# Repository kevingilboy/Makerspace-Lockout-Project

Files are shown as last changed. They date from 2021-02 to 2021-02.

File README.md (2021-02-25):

# Makerspace Lockout Project
Makerspace staff exert much of their time watching over students and verifying safety training… a process that is mundane, imperfect, and begs for automation.
Our motivation was to non-obtrusively enforce the safe and sustainable use of machinery in the Makerspaces across campus through RF student ID verification against a user database - if a student is not trained, power is cut to the tool and it will not turn on. If a student is trained, the tool is enabled.

[Video](https://www.youtube.com/watch?v=2HG-vyV4yoM)

[Poster](https://github.com/kevingilboy/Makerspace-Lockout-Project/blob/main/Design%20Expo%20Poster.pdf)

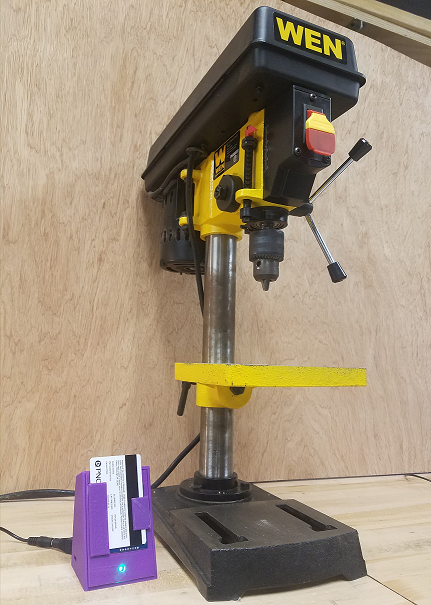
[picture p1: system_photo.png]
System Photo


## System Usage Diagram
The system is diagrammed below. A Raspberry Pi acts as a Wi-Fi access point and MQTT broker for Arduino microcontrollers in the Makerspace, and it communicates with the external database to authenticate users trying to enable tools. The complete workflow is as follows (please watch the [Video](https://www.youtube.com/watch?v=2HG-vyV4yoM) above for the simpler workflow. It is much easier to "show" this project than to "tell" about it).
1. A user inserts their ID into the 3D printed "Card Holder". The Holder holds the card such that the RFID element hovers over an RFID reader. A Wi-Fi Arduino inside the Holder detects that a card has been placed and reads the UUID from the student ID.
2. The Wi-Fi Arduino publishes a MQTT message to the Raspberry Pi in the room asking for user authentication, and notifies it which tool the user is trying to use. The Arduino changes a status LED to yellow to signify that authentication is underway.
3. The Pi asks the main Makerspace server if the user is authenticated for the given tool and the server responds.
4. An optional buddy system is also supported in that a tool can require a room administrator to put their card in a separate "buddy" Card Holder.
5. If authenticated (and a buddy is present if required), the Pi publishes a MQTT message to a separate Wi-Fi Arduino that controls power to the tool via a 120V relay. The Card Holder Arduino also receives this message and changes the status LED to green to signify that the user is authenticated.
6. The Arduino enables the tool through the relay and the user can do their work. The system can detect if the tool is prematurely switched on as it turns on the relay (e.g. if the previous person forgot to turn off the tool and simply grabbed their ID and left), and quickly switches the relay off as a failsafe. A buzzer makes noise to let the user know to switch off the tool for the relay to be enabled.
7. If a user leaves their ID on a Card Reader but does not power on the machine for a certain time threshold, an email is sent to them stating that they either forgot their ID on the Card Reader or are being unsafe by leaving tools enabled and unused for long periods of time.
8. When the user is finished, they take their ID off the Card Reader, which turns the status light to red and triggers a MQTT message from the Card Reader to the Pi, which then publishes a MQTT message to the relay-controlling Arduino to turn off the relay. If the user takes their ID off the reader without switching off the tool (as detected through current monitoring), a buzzer makes noise and power to the relay is cut.

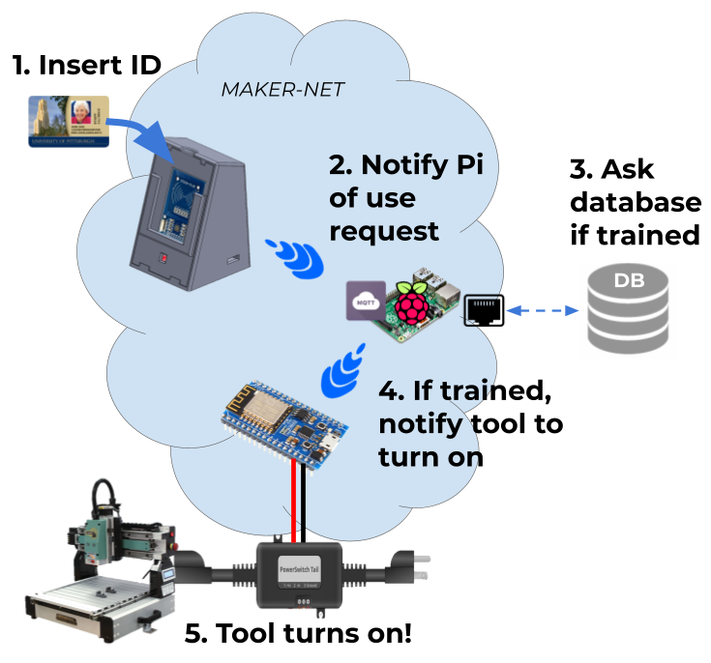
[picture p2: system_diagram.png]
System Diagram


## Materials for One Connected Tool
| Component | Quantity | Total Cost
| --- | --- | ---
| Wi-Fi Arduino MCU (ESP8266) | 2 | $20
| RFID Reader (MFRC522) | 1 | $5
| RGB LED (Adafruit Neopixel) | 1 | $1
| Relay (PowerSwitch Tail II) | 1 | $26
| Current Sensor (30A Split Core from Sparkfun) | 1 | $10
| Piezo Alarm (Optional) | 1 | $3
| Power supply for MCUs | 2 | $10
| Assorted jumpers | |
| PCB board | |
| 3D printer filament | |
| Some sort of metal lock box? | |
| | | $75

## Materials for One Connected Makerspace
| Component | Quantity | Total Cost
| --- | --- | -----
| Raspberry Pi 3 | 1 | $35
| 2A Wall Adapter Power Supply (USB Micro-B) |1 | $8
| | | $43

## State of the Repo
All arduino code has been uploaded

All EAGLE PCB CAD files have been uploaded

All SolidWorks CAD files have been uploaded

In-Room Pi Access Point files have been uploaded - SD card image available by request

The Database has been defined but the external server code has not been uploaded

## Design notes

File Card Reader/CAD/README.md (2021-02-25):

# CAD

There are three 3D-printable parts for the housing shown below, which was designed by BryanPatrick (baf56@pitt.edu).
- The body, which is a hollowed container with an exposed front meant to house the ESP8266 arduino and wiring. A slot is cutout on the top to allow removal of the pressfit lid (see below) and on the side to allow a power cord to reach the arduino.
- The lid, which is a pressfit cap for the hollow body. It has a slot for a neopixel and RFID reader to pressfit into. It also has slots for the U shape holder to pressfit into (see below)
- The U shape holder, which is meant to hold a student ID at the perfect height so that the embedded RFID element is aligned with the RFID sensor when seated in the holder. The bottom is open to allow sawdust or other particulate to fall right through.

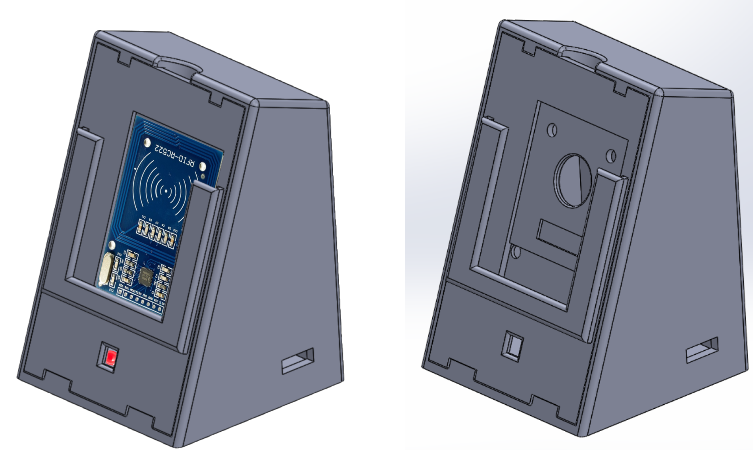
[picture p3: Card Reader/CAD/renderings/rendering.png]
Rendering


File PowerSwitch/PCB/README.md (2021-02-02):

# PCB

The PCB EAGLE CAD files are included here. The PCB was milled using an Othermill (Bantam CNC) with a 1/64" tool.

The ESP8266 arduino was soldered to this PCB, along with the current sensor, powertail relay, buzzer, and some resistors.

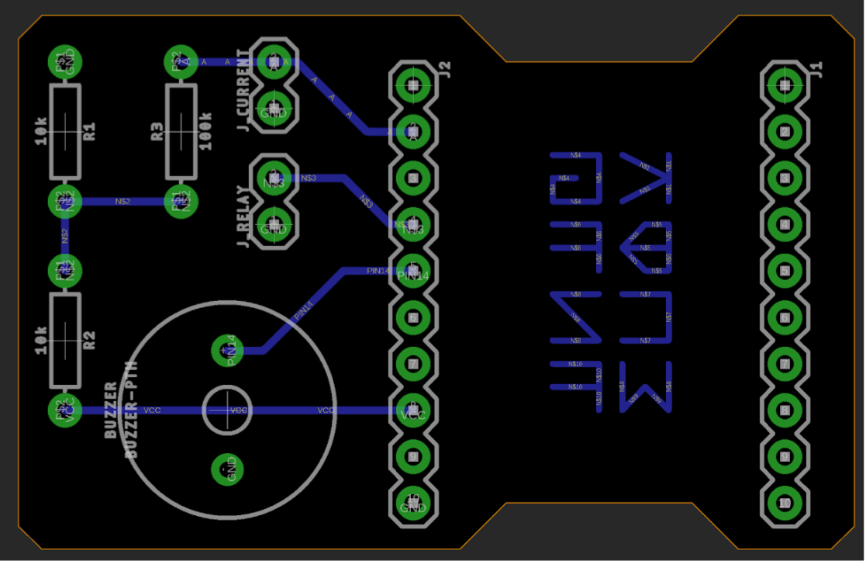
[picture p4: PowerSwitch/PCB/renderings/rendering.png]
Rendering


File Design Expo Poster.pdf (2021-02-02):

# LOCKOUT

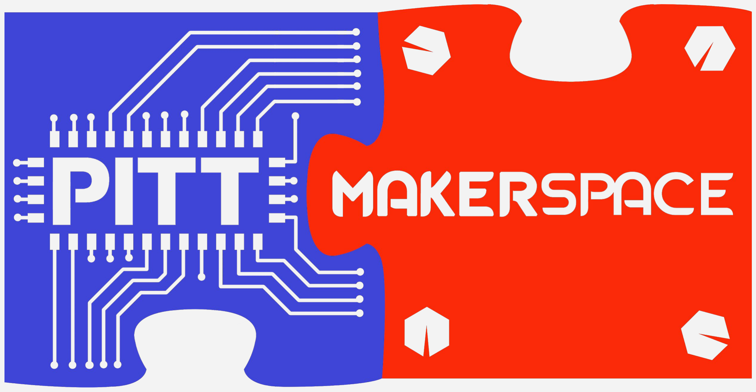
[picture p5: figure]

# An RFID Safety Enforcing Mechanism for SSOE Makerspaces and Machine Shops

## Kevin Gilboy, BryanPatrick Farren, Chen Zhu, Woodrow Fulmer

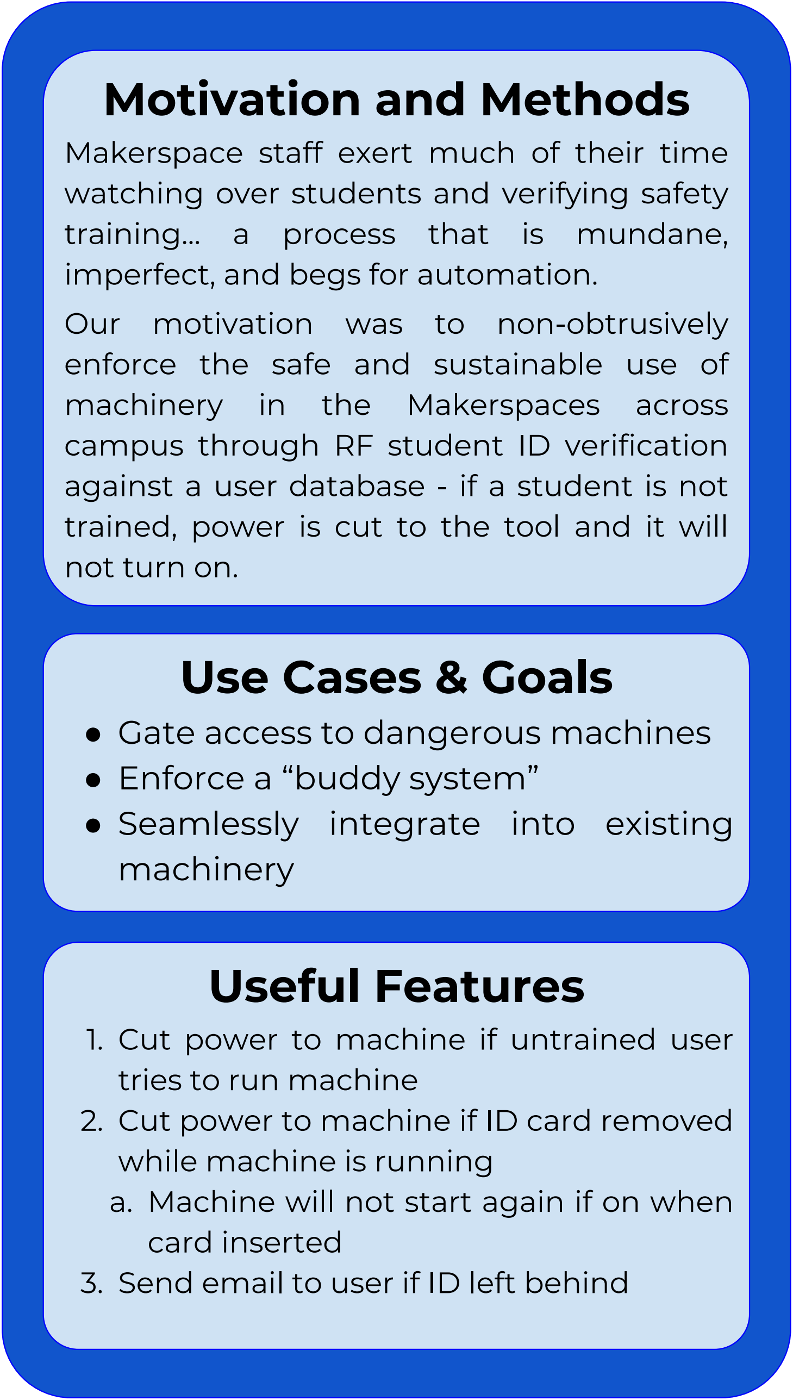
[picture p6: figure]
Motivation and Methods; training… a process that is mundane, imperfect, and begs for automation. Our motivation was to non-obtrusively enforce the safe and sustainable use of machinery in the Makerspaces across; not turn on.; Use Cases & Goals; ● Gate access to dangerous machines ● Enforce a “buddy system” ● Seamlessly integrate into existing machinery; Useful Features; tries to run machine; while machine is running; card inserted 3. Send email to user if ID left behind
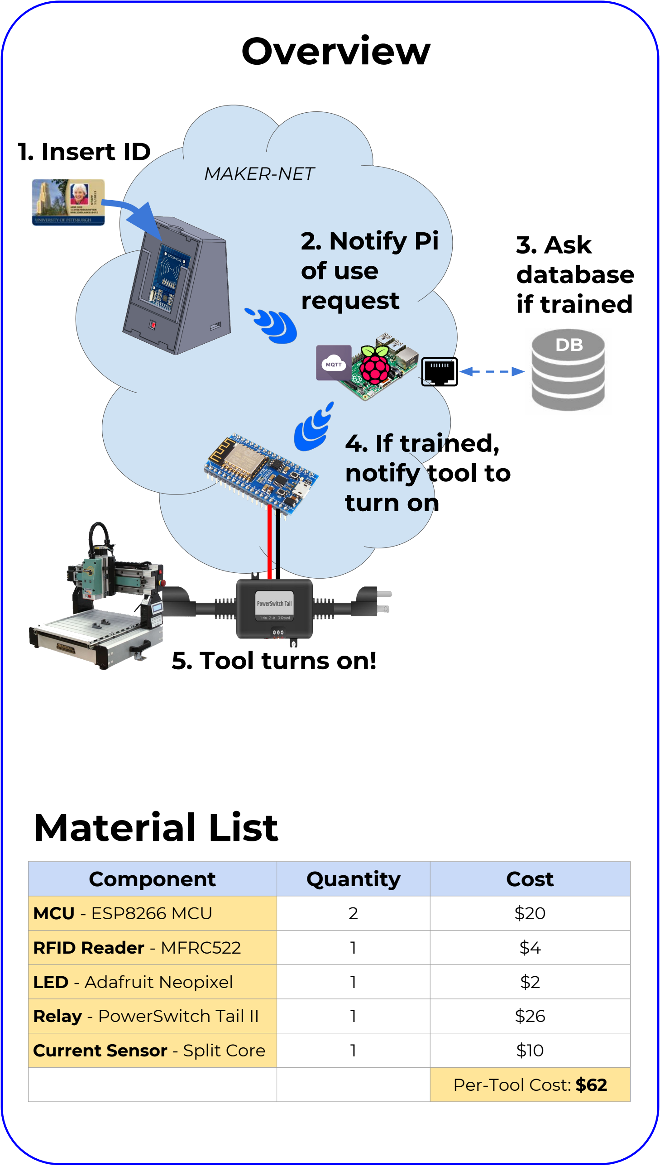
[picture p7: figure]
1. Insert ID; 2. Notify Pi of use request; 3. Ask database if trained; 4. If trained, notify tool to turn on; 5. Tool turns on!; MAKER-NET; Component; Quantity; Cost; MCU - ESP8266 MCU; RFID Reader - MFRC522; LED - Adafruit Neopixel; Relay - PowerSwitch Tail II; Current Sensor - Split Core; Per-Tool Cost: $62; Material List; Overview

Makerspace staff exert much of their time watching over students and verifying safety

campus through RF student ID verification against a user database - if a student is not trained, power is cut to the tool and it will

1. Cut power to machine if untrained user
2. Cut power to machine if ID card removed
a. Machine will not start again if on when

## User Feedback

The Lockout device has been installed in Makerspace MS1 for approximately 1 month. During that time, the MS1 staff have enjoyed its simplicity and ease of use, allowing them to show which volunteer is on duty. Soon they plan to use it as a ‘Master Switch’ for the Makerspace tools and machinery.

## Future Vision

Looking ahead, we aspire to expand to other locations across campus - including all three Makerspaces, plus the SCPI machine shop. Furthermore, our system could also be expanded to manufacturing factories and art studios.
We also aim to adapt a similar system for use with 3D printers and 220V tools, where
we | will | need | to | target | specific
points-of-interest to disable the tool (rather than a 120V relay).

## Acknowledgements

A special thank you to all those who helped out with this project: Dr. William Clark, Brandon Barber, The Makerspace Staff, Andy Holmes, and Jeff Speakman.

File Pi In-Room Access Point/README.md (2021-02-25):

# Pi In-Room Access Point

The In-Room access point serves as the Makerspace IoT orchestrator. It hosts a local and isolated WLAN for all devices in the Makerspace, receives MQTT messages about IDs being placed on card readers, it asks the remote server if users are authenticated for those tools and receives the response, and it sends MQTT messages to PowerSwitches to enable the relays connected to tools. It also sends emails in case of a tool timeout and can enforce the buddy system.

The NodeJS server app that runs on the Pi can be found in the `site` directory.

The Pi can either be created by flashing an image file or from scratch. The steps for starting from scratch are as follows:

## 1. Flash Raspbian to an SD card
I used [Raspbian Jessie](https://downloads.raspberrypi.org/raspbian/images/raspbian-2017-07-05/) since it was the most recent at the time and I am most familiar with it. I used Win32DiskImager to do the flashing.

## 2. Connect the Pi to Pitt internet over ethernet
I did this manually by modifying `/etc/network/interfaces` to assign the eth0 interface a static IP that the IT department provided for the given ethernet port. I provide the configuration file [here](https://github.com/kevingilboy/Makerspace-Lockout-Project/blob/main/Pi%20In-Room%20Access%20Point/etc/network/interfaces).

## 3. Create the local WLAN
1.  Install the needed packages\
`sudo apt-get install dnsmasq hostapd`
2. End the running instances of those packages\
`sudo systemctl stop hostapd`\
`sudo systemctl stop dnsmasq`\
`sudo service dhcpcd restart`
3. Edit `/etc/dnsmasq.conf`\
I provide the configuration file [here](https://github.com/kevingilboy/Makerspace-Lockout-Project/blob/main/Pi%20In-Room%20Access%20Point/etc/hostapd/hostapd.conf).
4. Edit `/etc/hostapd/hostapd.conf`
I provide the configuration file [here](https://github.com/kevingilboy/Makerspace-Lockout-Project/blob/main/Pi%20In-Room%20Access%20Point/etc/dnsmasq.conf)\
In this file, make sure to set the network SSID, password, and if the network should be hidden
5. Restart the services and interfaces\
`sudo service dhcp restart`\
`sudo ifdown wlan0`\
`sudo ifup wlan0`\
`sudo service hostapd start`\
`sudo service dnsmasq start`

## 4. Install the Mosquitto MQTT Broker
I followed [these](https://www.instructables.com/Installing-MQTT-BrokerMosquitto-on-Raspberry-Pi/) steps which consist of:\
`wget http://repo.mosquitto.org/debian/mosquitto-repo.gpg.key`\
`sudo apt-key add mosquitto-repo.gpg.key`\
`cd /etc/apt/sources.list.d`\
`wget http://repo.mosquitto.org/debian/mosquitto-repo.gpg.key`\
`sudo apt-get update`\
`sudo apt-get install mosquitto mosquitto-clients`

## 5. Ensure npm, nodejs, and nodemon are installed

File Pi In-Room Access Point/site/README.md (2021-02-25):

# Site
This is the Makerspace server app for communicating with ESP8266-connected RFID readers and tool power sources over MQTT. It includes support for an admin-based buddy system and sending emails when a tool times out.

Fields in `app.js` like the SSID, wifi password, database username, database password, email address, and email password were omitted and labelled with `// TODO` for clarity.

To run, first ensure that npm, nodejs, and nodemon are installed. Then use `npm install` to install the dependencies of the app. Once completed, the app can be started by `npm start`.

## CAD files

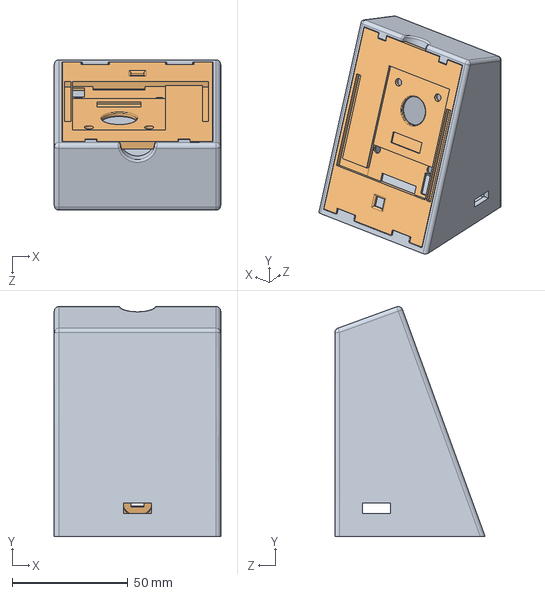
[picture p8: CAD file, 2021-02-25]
Card Reader/CAD/Assembly.SLDASM
72.0 x 99.4 x 65.0 mm
project1_t3
Project1_lid (ver.3.0)

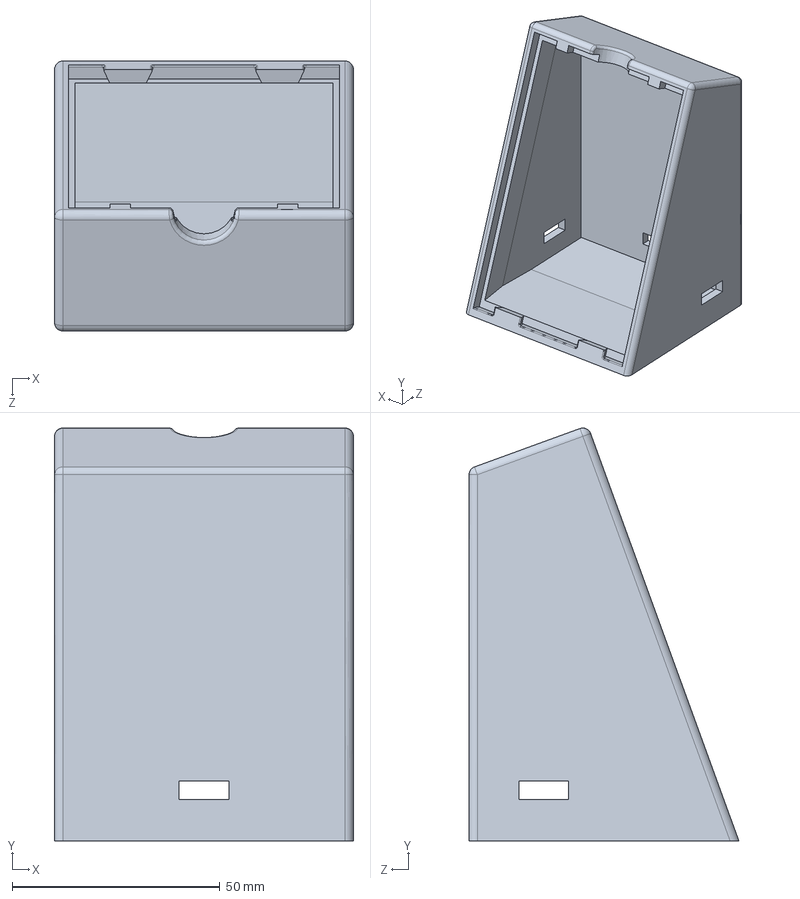
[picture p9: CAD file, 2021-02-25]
Card Reader/CAD/Body.SLDPRT
72.0 x 99.4 x 65.0 mm

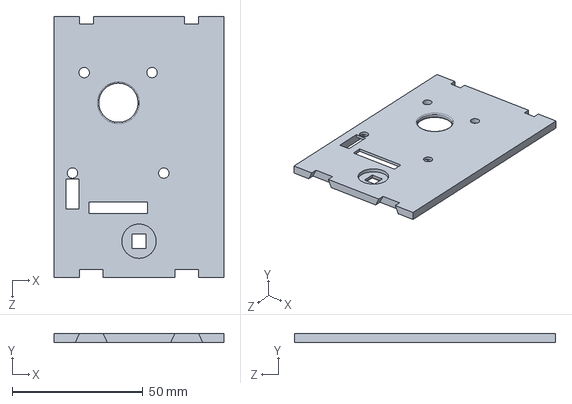
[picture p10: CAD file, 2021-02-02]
Card Reader/CAD/Lid(v3).SLDPRT
65.0 x 3.50 x 100.0 mm

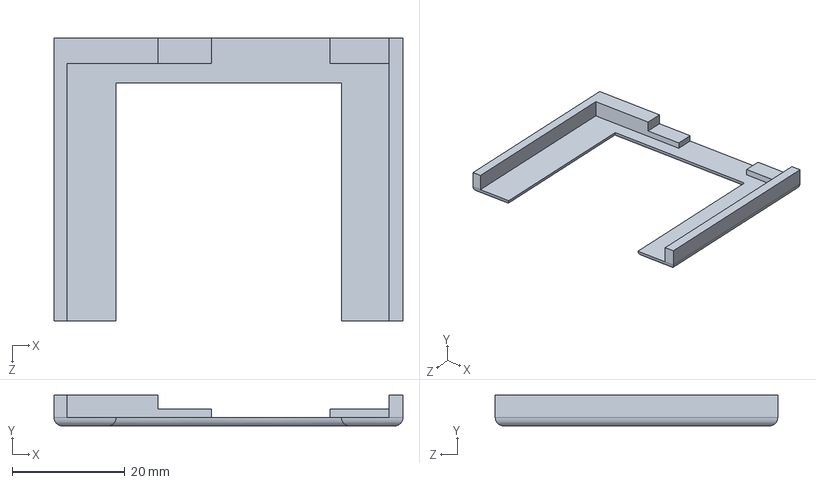
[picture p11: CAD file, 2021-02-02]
Card Reader/CAD/U_Shape_Holder.SLDPRT
62.0 x 5.50 x 50.2 mm

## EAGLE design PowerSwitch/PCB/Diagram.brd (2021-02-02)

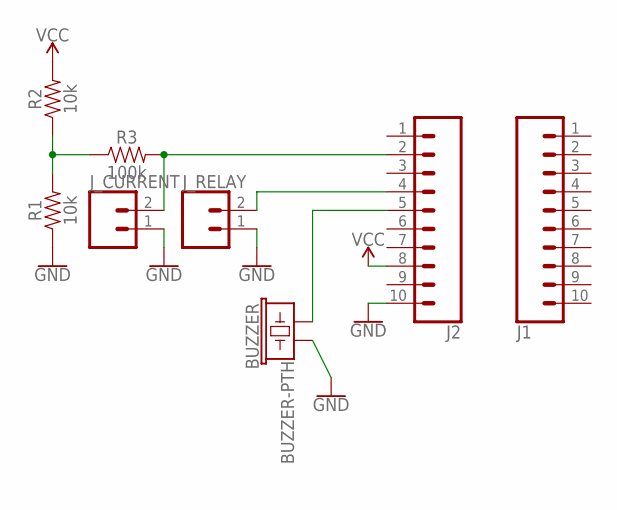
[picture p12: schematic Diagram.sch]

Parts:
BUZZER: BUZZER-PTH; BUZZER-12MM
J1, J2: CONN_10"; 1X10
J_CURRENT: CONN_02; 1X02
J_RELAY: CONN_02; 1X02
R1, R2: 10k; AXIAL-0.3
R3: 100k; AXIAL-0.3

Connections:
A: J2.2, J_CURRENT.2, R3.P$2 (2)
GND: BUZZER.- (2), J2.10, J_CURRENT.1, J_RELAY.1, R1.P$1 (1)
unnamed: R1.P$2 (2), R2.P$1 (1), R3.P$1 (1)
unnamed: J2.4, J_RELAY.2
PIN14: BUZZER.+ (1), J2.5
VCC: J2.8, R2.P$2 (2)

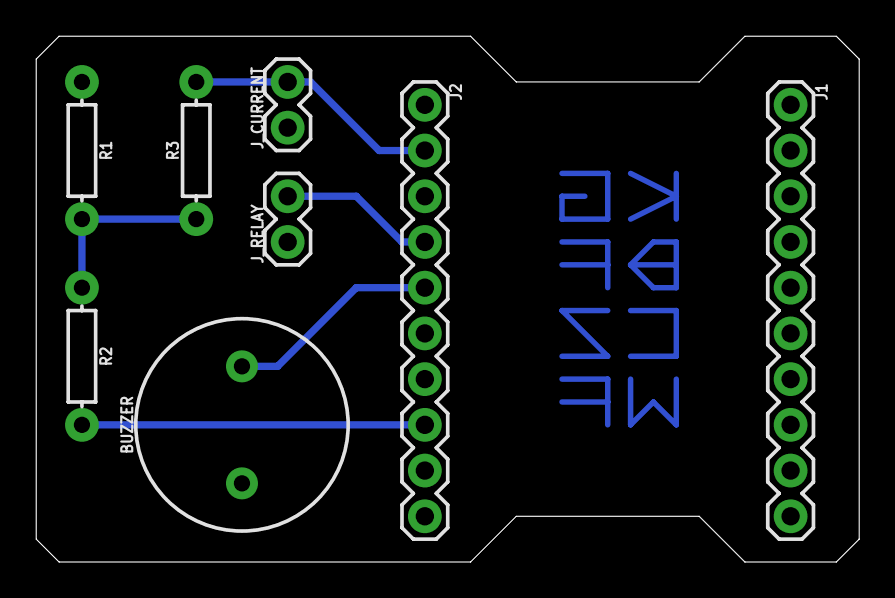
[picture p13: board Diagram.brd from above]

Board: 2 copper layers, 45.7 x 29.2 mm, 8 parts (0 on the bottom side), 6 nets.

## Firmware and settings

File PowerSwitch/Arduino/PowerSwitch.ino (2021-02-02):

// Kevin Gilboy 2018
// Pitt Makerspace

#include <ESP8266WiFi.h>
#include <PubSubClient.h>

// Unique identifier of this tool. Must be the same name used by the
// Card_Reader_For_Tools.ino code uploaded to the card-reading arduino.
#define TOOLNAME "ms1_drill_press"

// If we do not have a current sensor on hand, set this to false
#define CHECK_CURRENT true

// Some tweakable defined parameters
#define TOOL_TIMEOUT 30000
#define CURRENT_THRESHOLD 200
#define DELAY_BEFORE_FIRST_READING 7500
#define DELAY_BETWEEN_READINGS 6667
#define NUMBER_OF_READINGS 4
#define NUMBER_OF_BUZZES 3
#define PITCH_OF_BUZZES 64

// Define the pins for I/O
#define LED_PIN 0
#define BUZER_PIN 14
#define RELAY_PIN 16
#define CURRENT_PIN A0

// Store the wifi credentials and mqtt server IP
const char* ssid = "ssid";
const char* password = "PASSWORD";
const char* mqtt_server = "192.168.0.1";

// Wifi/MQTT comms variables
WiFiClient espClient;
PubSubClient client(espClient);
char recmsg[127];

// State variables
bool sent_email = false;
int tool_on = true;
unsigned long last_time_off = millis();
bool card_in_reader = false;
int readings[NUMBER_OF_READINGS];

//
// Sets up wifi
//
void setup_wifi() {
  delay(10);
  // We start by connecting to a WiFi network
  Serial.println();
  Serial.print("Connecting to ");
  Serial.println(ssid);

  WiFi.begin(ssid, password);

// Wait for connection
  while (WiFi.status() != WL_CONNECTED) {
    delay(500);
    Serial.print(".");
  }

  Serial.println("");
  Serial.println("WiFi connected");
  Serial.println("IP address: ");
  Serial.println(WiFi.localIP());
}

//
// Callback for any received MQTT message
//
void callback(char* topic, byte* payload, unsigned int length) {
    // Copy the message into a char buffer
    for (int i=0; i<length; i++) {
      recmsg[i] = (char)payload[i];
    }

    // The action we are interested in is in the first few characters. Either "off" or "on"
    if (strncmp(recmsg,"off",3)==0){
      // If msg says off (likely because a user removed their ID from the reader), turn off the tool.
      Serial.println("Turning off");
      card_in_reader = false;

      //If user removed ID without turning off tool, buzz at 'em
      if (CHECK_CURRENT) {
        if (current_detected()) {
          buzz();
        }
      }

      //Turn off powerswitch
      turn_off();
      tool_on = false;
    } else if (strncmp(recmsg,"on",2)==0) {
      // If msg says on (likely because an authenticated user put their ID on the reader), turn on the tool
      Serial.println("Turning on");
      card_in_reader = true;
      sent_email = false; // reset this flag

      //Turn on powerswitch
      turn_on();
      tool_on = true;

      if (CHECK_CURRENT) {
        //If tool was left in the on state (i.e. a current is detected immediately), buzz at 'em
        // Keep trying to turn enable the relay, switching it off if current is detected
        while (current_detected()) {
          turn_off();
          if(!card_in_reader) break;
          buzz();
          client.loop(); // Need to call this to not block any new messages sent by the server
          turn_on();
        }
      }
    }
}

//
// Reconnect to MQTT server
//
void reconnect() {
  // Loop until we're reconnected
  while (!client.connected()) {
    Serial.print("Attempting MQTT connection...");
    // Attempt to connect
    if (client.connect(TOOLNAME"_powertail")) {
      Serial.println("connected");
      // ... and resubscribe
      client.subscribe("makermqtt/"TOOLNAME);
    } else {
      Serial.print("failed, rc=");
      Serial.print(client.state());
      Serial.println(" try again in 5 seconds");
      // Wait 5 seconds before retrying
      delay(5000);
    }
  }
}

//
// Detect current from the current sensor
//
bool current_detected() {
  int zeros = 0;
  int below_noise_threshold = 0;

  delayMicroseconds(DELAY_BEFORE_FIRST_READING-DELAY_BETWEEN_READINGS);
  // Take multiple readings
  for (int i=0;i<NUMBER_OF_READINGS;i++) {
    delayMicroseconds(DELAY_BETWEEN_READINGS);
    readings[i] = analogRead(CURRENT_PIN);
    if(readings[i]>CURRENT_THRESHOLD) return true;
    if(readings[i]==0) zeros++;
    if(readings[i]<=32 && readings[i]>0) below_noise_threshold++;
  }

  // This is a tuned condition that determines if current has been detected. Based on power consumption of the tool, this may need tweaking for new tools
  if((zeros==NUMBER_OF_READINGS-1 && below_noise_threshold==1) || zeros==NUMBER_OF_READINGS) return true;
  return false;
}

//
// Buzz at em'
//
void buzz() {
  for(int i=0;i<NUMBER_OF_BUZZES;i++){
    analogWrite(BUZER_PIN,64);
    delay(250);
    analogWrite(BUZER_PIN,0);
    delay(250);
  }
}

//
// Turn off the tool relay and onboard LED
//
void turn_off(){
  digitalWrite(LED_PIN,LOW);
  digitalWrite(RELAY_PIN,LOW);
}

//
// Turn on the tool relay and onboard LED
//
void turn_on(){
  digitalWrite(LED_PIN,HIGH);
  digitalWrite(RELAY_PIN,HIGH);
}

void setup() {
  // Initialize the BUILTIN_LED pin as an output
  pinMode(LED_PIN, OUTPUT);
  pinMode(RELAY_PIN, OUTPUT);

  // Make sure the relay and buzzer start off
  turn_off();
  analogWrite(BUZER_PIN,0);

  // Begin Serial for debugging
  Serial.begin(115200);

  // Connect to Wifi and configure mqtt server/callback
  setup_wifi();
  client.setServer(mqtt_server, 1883);
  client.setCallback(callback);
}

void loop() {
  // Reconnect to MQTT if not connected
  if (!client.connected()) {
    reconnect();
  }

  // If current sensing is enabled
  if (CHECK_CURRENT) {
    // If an authenticated card is in the corresponding reader
    if (card_in_reader) {
      // If tool being used, keep delaying last_time_off so an email isn't sent
      if(current_detected()){
        last_time_off = millis();
        tool_on = true;
      } else if(tool_on){
        // If tool is not being used but is in the on state, save the time so that we know when to alert the user that they left their ID behind
        last_time_off = millis();
        tool_on = false;
      }

      //If it has been longer than a set amount of time, emit "timeout" signal to server
      // Since it is unsigned subtraction we do not have to worry about millis() resetting
      if((unsigned long)(millis()-last_time_off)>=TOOL_TIMEOUT && !sent_email){
        client.publish("makermqtt/"TOOLNAME,"timeout");
        sent_email = true; // set this flag so that we do not send emails on every loop
      }
    }
  }

  delay(2000);
  client.loop();
}

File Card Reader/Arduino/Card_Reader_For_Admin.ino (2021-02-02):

// Kevin Gilboy 2018
// Pitt Makerspace

#include <SPI.h>
#include <MFRC522.h>
#include <ESP8266WiFi.h>
#include <PubSubClient.h>
#include <Adafruit_NeoPixel.h>
#ifdef __AVR__
  #include <avr/power.h>
#endif

// Unique identifier of this makerspace
#define TOOLNAME "ms1_volunteer"

// Define some colors and which LED we will be using
#define RED pixels.Color(63,0,0)
#define BLUE pixels.Color(0,0,63)
#define GREEN pixels.Color(0,63,0)
#define YELLOW pixels.Color(63,31,0)
#define LED 0

// Define the pins for the RFID reader
#define RST_PIN   4     // Configurable
#define SS_PIN    5    // Configurable

// Create MFRC522 instance
MFRC522 mfrc522(SS_PIN, RST_PIN);

// Create neopixel instance
Adafruit_NeoPixel pixels = Adafruit_NeoPixel(1, 15);

// Store the wifi credentials and mqtt server IP
const char* ssid = "SSID";
const char* password = "PASSWORD";
const char* mqtt_server = "192.168.0.1";

// Wifi/MQTT comms variables
WiFiClient espClient;
PubSubClient client(espClient);
char recmsg[127];
char sendmsg[127];
char uid[9];

// State variables
int card_in_slot = false;
int powerswitch_status = 0; // this could be a bool but its easier to keep as an int since its sent to the server in a string

//
// Sets LED color
//
void setLED(uint32_t c){
  pixels.setPixelColor(0,c);
  pixels.show();
}

//
// Sets up wifi
//
void setup_wifi() {
  delay(10);
  // We start by connecting to a WiFi network
  Serial.println();
  Serial.print("Connecting to ");
  Serial.println(ssid);

  // Show blue while we are connecting
  setLED(BLUE);
  WiFi.begin(ssid, password);

  // Wait for connection
  while (WiFi.status() != WL_CONNECTED) {
    delay(500);
    Serial.print(".");
  }

  // Once connected, show red, which means the tool is disabled and we are waiting on an ID to be inserted
  setLED(RED);
  Serial.println("");
  Serial.println("WiFi connected");
  Serial.println("IP address: ");
  Serial.println(WiFi.localIP());
}

//
// Callback for any received MQTT message (not used for admin card reader)
//
void callback(char* topic, byte* payload, unsigned int length) {

}

//
// Reconnect to MQTT server
//
void reconnect() {
  // Loop until we're reconnected
  while (!client.connected()) {
    // Show blue while reconnecting
    setLED(BLUE);
    Serial.print("Attempting MQTT connection...");
    // Attempt to connect
    if (client.connect(TOOLNAME"_rfid")) {
      Serial.println("connected");
    } else {
      Serial.print("failed, rc=");
      Serial.print(client.state());
      Serial.println(" try again in 5 seconds");
      // Wait 5 seconds before retrying
      delay(5000);
    }
  }

  // Once reconnected, show red
  setLED(RED);
}

void setup() {
  // Initialize the BUILTIN_LED pin as an output
  pinMode(LED, OUTPUT);
  digitalWrite(LED,HIGH);
  pixels.begin();

  // Begin Serial for debugging
  Serial.begin(115200);

  // Connect to Wifi and configure mqtt server/callback
  setup_wifi();
  client.setServer(mqtt_server, 1883);
  client.setCallback(callback);

  // Init the RFID reader
  SPI.begin();
  mfrc522.PCD_Init();
  mfrc522.PCD_SetAntennaGain(112); //Increase antenna gain
}

void loop() {
  // Reconnect to MQTT if not connected
  if (!client.connected()) {
    reconnect();
  }

  // If a new card has been detected on the reader
  if(mfrc522.PICC_IsNewCardPresent() && mfrc522.PICC_ReadCardSerial()) {
    // Make sure a card is not in the slot already (this should always be satisfied)
    if(!card_in_slot) {
      card_in_slot = true;
      Serial.println("Card detected");

      // Send server a message with all necessary info to authenticate user.
      sprintf(uid,"%02X%02X%02X%02X\0",mfrc522.uid.uidByte[0],mfrc522.uid.uidByte[1],mfrc522.uid.uidByte[2],mfrc522.uid.uidByte[3]);
      sprintf(sendmsg,"{\"toolname\":\"%s\",\"uid\":\"%s\"}",TOOLNAME,uid);
      client.publish("makermqtt/rfid/admin_card_detected",sendmsg);

      setLED(YELLOW);
      delay(500);
      setLED(GREEN);
    }
  }
  // Else, if a card has been removed from the reader
  else if(!mfrc522.PICC_IsNewCardPresent() || !mfrc522.PICC_ReadCardSerial()){
    // Make sure a card was on the slot already (this should always be satisfied)
    if(card_in_slot){
      card_in_slot = false;

      Serial.println("Card removed");

      // Send server a message with all necessary info to terminate the volunteer's session
      sprintf(sendmsg,"{\"toolname\":\"%s\",\"uid\":\"%s\"}",TOOLNAME,uid);
      client.publish("makermqtt/rfid/admin_card_removed",sendmsg);

      setLED(YELLOW);
      delay(500);
      setLED(RED);
    }
  }

  delay(50);
  client.loop();
}

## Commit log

2021-02-02 Added ID holster CAD
    [Lid (V3.0.0).SLDPRT, U shape holder.SLDPRT]
2021-02-02 Added ID holster arduino code
2021-02-02 Renamed folder to Card Reader
    [Lid (V3.0.0).SLDPRT, U shape holder.SLDPRT]
2021-02-02 Added PCB files
    [Diagram.brd, Diagram.sch]
2021-02-02 Added PowerSwitch arduino
2021-02-02 Changed name of PowerSwitch directory
    [Diagram.brd, Diagram.sch]
2021-02-02 Fixing directory naming
    [Diagram.brd, Diagram.sch]
2021-02-02 Re-added PowerSwitch directory
    [Diagram.brd, Diagram.sch]
2021-02-25 Added all card reader CAD files
    [Assembly.SLDASM, Body.SLDPRT, Lid(v3).SLDPRT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]

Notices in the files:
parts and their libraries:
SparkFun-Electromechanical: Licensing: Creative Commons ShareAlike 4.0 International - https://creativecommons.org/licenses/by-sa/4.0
